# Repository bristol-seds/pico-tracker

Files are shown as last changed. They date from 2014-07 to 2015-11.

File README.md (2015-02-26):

## Bristol SEDS Pico Tracker ##

Gets its GPS position home by whatever means possible, come hell or
high water.

(Actually, come low temperatures, long paths, geopolitical
restrictions, low power etc.)

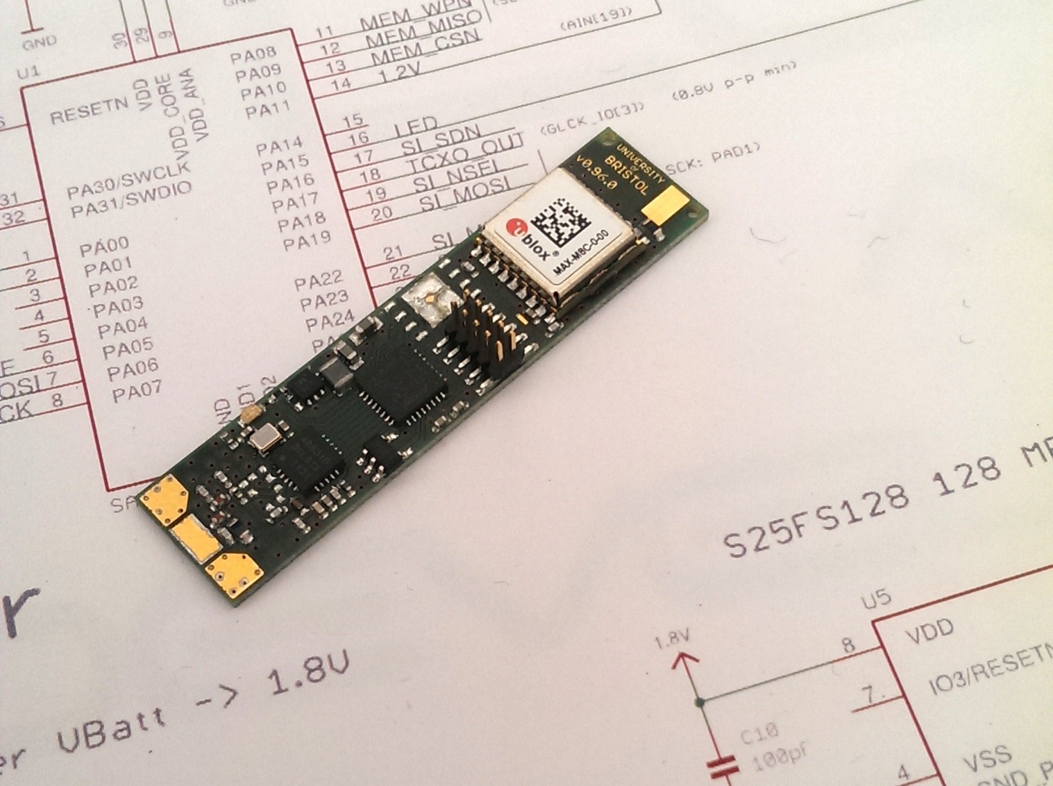
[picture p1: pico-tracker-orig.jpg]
Photo of second board revision


## Test Flight

On 31st August 2014.

## [Parts List](hardware/Parts.md)

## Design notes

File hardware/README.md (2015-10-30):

#### Hardware Revisions

Most hardware that has been built has a version number

|Version|Description|Exists/Existed|Flights used on
|----|----|----|----
|v0.96.0|Original AAA Battery. Flown with modifications to connect tcxo to mcu.|x|UBSEDS3-8?
|v0.981.0|Solar Power SPV1040. Flown with modifications simplify power circuit.|x|UBSEDS9
|v0.981.1|Minor fixes|
|v0.982.0|AAA Battery. Never fully populated, used for lab testing.|x|
|v0.982.1|Minor fixes|
|v0.984.0|First attempt at internal balloon board|
|v0.985.0|Solar Power/Primary AAA Lithium|x|UBSEDS10-11
|v0.985.1|Added DNP/0Ω between solar and MPPT set for use when only a battery is connected|
|v0.985.2|BMP180 -> MS5607 Pressure / Temperature Sensor|
|v0.985.3|Smaller holes for external thermistor|
|v0.986.0|Low Power with side mounting GPS chip antenna|
|v0.986.9|Low Power. 80x80mm Breakout|

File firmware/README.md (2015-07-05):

## Bristol Pico Tracker ##

Firmware for the Bristol Pico Tracker. Gets its GPS position home
by whatever means possible, come hell or high water.

(Actually, come low temperatures, long paths, geopolitical
restrictions, low power etc.)

## Technical Description ##

The firmware is written in C and targeted at the highly configurable
Atmel SAMD20 series of ARM Cortex M0+ micromontrollers. The code can
be built using
[GNU Tools for ARM Embedded Processors](https://launchpad.net/gcc-arm-embedded/).
See [README-samd20-gcc-blackmagic.md](README-samd20-gcc-blackmagic.md)
for more details.

## Test Suite ##

The test suite is used to run test cases on real hardware. Test cases
are written mostly in python and run using a gdb that has been built
`--with-python`. It is still a work in progress but is quite handy
when debugging.

See [test/README.md](test/README.md) for more details.

## Sources & Licensing ##

See [LICENSE.md](LICENSE.md)

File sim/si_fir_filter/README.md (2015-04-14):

## Design of the Si TX Spectral Shaping Filter

The SI contains a 17-tap digital FIR filter for use in GFSK modes.

We use this in aprs mode to filter the gpio squarewave into a sensible
afsk signal.

There's some notes in a ipython notebook `si_fir_filter.ipynp` on
this. This notebook is also used to calculate the deviation values.

## Prerequisites

```
sudo apt-get install ipython libblas-dev liblapack-dev gfortran
pip install scipy matplotlib
```

Yes you need a fortran compiler!!!

## Python Usage

`ipython notebook`

## Calcuating new coefficients

There's an awesome calculator here
[here](http://t-filter.appspot.com/fir/index.html)

## So

The python script is from
[here](http://nbviewer.ipython.org/github/unpingco/Python-for-Signal-Processing/blob/master/Filtering.ipynb)

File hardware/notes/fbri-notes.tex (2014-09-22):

\documentclass[12pt]{article}
\usepackage{graphicx}
\usepackage{color}
\usepackage{fixltx2e}
\usepackage{datatool}
\usepackage{float}
%\usepackage[showframe=true]{geometry}
\addtolength{\textwidth}{1in}
\addtolength{\textheight}{1in}
\addtolength{\evensidemargin}{0.5in}
\addtolength{\oddsidemargin}{-0.5in}
\addtolength{\topmargin}{-0.5in}
\setlength{\parindent}{0cm}

\begin{document}

\section{Hardware}

The hardware exists in two versions: a minaturised version intended
for flight and a development version intended for firmware
developement and debugging etc. The two verisons share the same
circuit diagram, and hence firmware should be generally interoperable
between the two.

However to allow detection of the hardware version PA02 is shorted to
ground on the development version while is will be pulled high
internally on the flight version.

\subsection{Dimensions}

The flight hardware has a total size of 50 x 12 mm.

Components are positioned on a 1/16 (0.0625) mm grid, with major
components on a 1/4 mm grid.

\subsection{Routing}

The board is routed with 6 mil traces for data and 6 / 16 mil traces
for power. Where nessesary the traces  All via are 0.3mm (12mil) drill.

\section{Components}

\subsection{Development}

\section{Design}

\subsection{GPS}

\subsection{ESD Proctection}

The GPS Antenna input is particularly sensitive to ESD damage. Options
for protecting against this are outlines in the uBlox hardware
intergration manual \bibitem{ublox8hw}

 One
option to protect against this is to use an LNA with integrated ESD
protection, such as.

\subsection{TCXO}

Flight UBSEDS2 clocked the Si4060 directly from a 16 MHz crystal
osciallator. This was with about 6.5pF of internal capactance from the
Si4060.

\subsection{HF Clock}

This is synthesised in the SAM D20E and used to drive the XIN input of
the SI4060. The design frequency for the XIN input is 25 - 32MHz
(30MHz by default) but UPU reports success with 16.369MHz. The maximum
output clock frequency from the SAM D20E is 48MHz so this would be a
useful design limit.

No input capacitance value is given for the XIN pin but 2pF typical is
given for out pins and this is probably about the same.

The maximum rise/fall time for 48MHz is 10ns, around 5ns would be
good, giving a knee = 100MHz.

Path inductance is maybe 10nH total (1+1+1 x 2 for pad/gnd-pad/via, 4
for trace)

Maximum output current from the SAM D20E is 1mA (with DRVSTR=0, 1.8V),
so output impedance = 1800Ω

Worst case Q
\begin{equation}
  Q = {\sqrt{10nH/2pF} \over 100} = 0.22 (good)
\end{equation}

Time constant
\begin{equation}
  tc = RC = 1800*2pF = 3.6ns (good)
\end{equation}

In any case the SI4060 tune API allows ramping up the internal
capacitance to 11pF, which will drop Q at the expense of the time
constant.

\subsection {Firmware}

Check flight WG2 on habhub for gps string formatting gone wrong

Get so much test data.

\begin{thebibliography}{9}

\bibitem{ublox8hw}
  uBlox 8 Hardware integration manual,
  http://www.u-blox.com/images/downloads/Product_Docs/MAX-M8_HardwareIntegrationManual_(UBX-13004876).pdf

\end{thebibliography}

\end{document}

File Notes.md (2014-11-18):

## PCB Weight ##

The density of FR4 is 1,850 kg/m^3. If we assume a PCB area of 12*50 =
600 mm^2...

For a 1.0mm PCB: 600 * 1.0 * 1.85 = 1.110g
For a 1.6mm PCB: 600 * 1.6 * 1.85 = 1.728g

## Contestia ##

There doesn't appear to be much documentation for contestia...

[Oh here's some](http://f1ult.free.fr/DIGIMODES/MULTIPSK/contestia_rttym_en.htm)

Really we're looking at Olivia MFSK - contestia is just a variant.

[Wikipedia](http://en.wikipedia.org/wiki/Olivia_MFSK)
[ARRL](http://www.arrl.org/olivia)

It's already implemented in dl-fldigi [here](https://github.com/jamescoxon/dl-fldigi/blob/master/src/include/jalocha/pj_mfsk.h)

(Inverse) Fast Hadamard Transform needed

## APRS ##

[some description..](http://dooce.de/dokuwiki/doku.php?id=projekte:utrak:aprs)

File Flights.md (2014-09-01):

## UBSEDS2

Launched from EMF 31/08/2014. Joint flight with CUSF (JOEY rtty/turbo)
and SUSF (UKHAS repeater).

AAA battery and surgically attached 16MHz crystal. Measured 80mA
current draw, no power saving for the ublox 6.

Revision C Atmel SAM D20 microcontrollor (bit-banged SPI)

140g free lift on a 100g Hwoyee.

4 hours battery life, much less than expected. Low temperatures?

Watchdog enabled, 64 seconds timeout (based on ULP32k oscillator, so
+-50%)

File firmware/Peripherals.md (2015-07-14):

## SAM D20 Peripherals usage

| Type | Peripheral | Function | Notes
| --- | --- | --- | ---
|*GLCK*|
||gclk0|main clock, internal osc8m|4 MHz
||gclk1|tcxo clock, fed from xosc OR osc8m
||gclk7|aprs clock, fed from gclk1, div 6 / 11
|
|*TC*||
||tc0|telemetry tick timer. 32-bit. glck1
||tc1|^^^^^
||tc2|counts cycles of tcxo. 32-bit. gclk1
||tc3|^^^^^
||tc4|unused (osc8m event source)
||tc5|telemetry pwm 16-bit glck0, ALSO aprs carrier 16-bit gclk7
|
|*EXTINT*|
||extint[5]|gps timepulse
|
|*event channels*|
||0|event source for timer 2 xosc measurement
||1|tc4 retrigger
|
|*SERCOM*||
||sercom0|spi flash
||sercom1|ublox gps
||sercom2|
||sercom3|radio|currently bitbanged as required pin layout broken in sercom

## SAM D20 Interrupts usage

| Name | Function | Priority H(0-3)L | Notes
| --- | --- | --- | ---
|TC0_IRQn|telemetry tick timer|1|latency critical for symbol timing. rate <= 1200Hz
|[GPS_SERCOM]_IRQn|gps usart rx|2|latency not so critical. rate <= 960Hz
|EIC_IRQn|timepulse|3|latency not so critical. rate = 1
|TC2_IRQn|xosc measurement done|3|latency not critical
|ADC_IRQn|adc measurement done|3|latency not critical

## Clock Layout

```
[osc8m] --> [glck0] +
                    |--> [tc5]
                    |--> [adc]
                    |--> [extint]
                    |--> [cm0+, apbs etc.]

                     |\
         [osc8m]--> 0| |
                     | | --> [glck1] +--> [tc0, telemetry tick]
tcxo --> [xosc] --> 1| |             |--> [tc2, count tcxo] <-- gps timepulse
                     |/              |--> [glck7] --> [tc5] --> si_gpio1
                      |              |--> [gps usart]
                 *USE_XOSC*

[osculp32k] --> [gclk4] --> [wdt]
```

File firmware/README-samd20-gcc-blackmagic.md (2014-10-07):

## samd20-gcc-blackmagic ##

A simple GCC setup for Atmel SAM D20 development, intended for use with the
[blackmagic debug probe](https://github.com/gsmcmullin/blackmagic).

## Prerequisites ##

[GNU Make](http://www.gnu.org/software/make/) and the following
standard utilities are required: `cat`, `echo`, `find`, `grep`,
`mkdir`, `rm`, `sed` and `tr`. If you're running any sensible desktop
linux then these will already be installed.

You will also need to aquire
[GNU Tools for ARM Embedded Processors](https://launchpad.net/gcc-arm-embedded/).

##### On Ubuntu

```
sudo add-apt-repository ppa:terry.guo/gcc-arm-embedded
sudo apt-get update && sudo apt-get install gcc-arm-none-eabi
```

###### Note about gcc-arm-embedded on Ubuntu 14.04 and later

If you are using Ubuntu 14.04 and later, please be careful because
there are packages with same name but produced by Debian and inherited
by Ubuntu. Simply follow the above 3 steps, you may end up with
gcc-arm-none-eabi from Ubuntu. So to install gcc-arm-none-eabi from
ARM, steps are:

```
1). sudo apt-get remove binutils-arm-none-eabi gcc-arm-none-eabi
2). sudo add-apt-repository ppa:terry.guo/gcc-arm-embedded
3). sudo apt-get update
4). sudo apt-get install gcc-arm-none-eabi=4-8-2014q2-0trusty10
```
Meanwhile we are working with Debian to consolidate and unify this toolchain.

## Usage ##

### Project Options ###

[`config.mk`](config.mk) allows configuation for individual
projects. In particular the `PROJECT_NAME` and `TARGET_CHIP` variables
needs to be set.

### Compiling ###

`make`

## Backmagic ##

### Download ###

Run `arm-none-eabi-gdb`. If you have set `BLACKMAGIC_PATH` in
[`config.mk`](config.mk) then gdb will attempt to connect to the
blackmagic debugger. Otherwise you can use the `blackmagic` command to
connect a `/dev/ttyACM<n>` device. For example `blackmagic 0` will
connect to a blackmagic at `/dev/ttyACM0`.

To attach to the SAM D20 chip itself you will need to run something like

```
monitor swdp_scan
attach 1
```

You can place these commands in a `gdbscript-custom` file so that in
future they will be run automatically. If `monitor swdp_scan` fails to
detect an attached SAM D20 device then you may need to upgrade the
firmware on your blackmagic to the latest version.

To download code run

```
monitor erase_mass
load
```

### Debugging ###

You can start with the gdb command

```
run
```

You might want to use the command `set confirm off` so that you're not
prompted each time. You might also want to `set mem
inaccessible-by-default off` so that you can look at memory locations
outside of RAM and ROM.

These commands can be automated by placing them in a `gdbscript-custom` file.

### Semihosting ###

You can build for semihosting by defining the `SEMIHOSTING` variable
in make. Like this:

```
make -kB SEMIHOSTING=1
```

This build will be significantly larger (in terms of RAM and ROM).

For this build, when a debugger is present at startup the
`semihost_printf`, `semihost_puts` and `semihost_putchar` functions
will print to stdio on the host. The Blackmagic Debug Probe supports
this.

## Emacs ##

The command `make emacs` can be used to quickly launch an instance of
emacs with all the relavent source code loaded.

A `TAGS` file can be generated with `make all` or `make tags`, and
this can be used to automat navigate the source code. See the
[emacs manual](https://www.gnu.org/software/emacs/manual/html_node/emacs/Tags.html)
for more details.

A Directory Local Variables File [`.dir-locals.el`](.dir-locals.el)
exists in the root of the project. This has the following effects
on emacs:

### Fixed default-directory ###

The default directory is fixed as the root of the project wherever you
are within the project. As the makefile needs to be run from the root
of the project, this means that `M+x compile` will always run the
top-level makefile no matter which file you are editing.

### Custom GDB ###

`M+x gdb` is set to use `arm-none-eabi-gdb` rather than the default GDB for your
machine.

## Other notes ##

Wherever possible use
[Function Attributes](http://gcc.gnu.org/onlinedocs/gcc/Function-Attributes.html)
and
[Variable Attrubutes](http://gcc.gnu.org/onlinedocs/gcc/Variable-Attributes.html)
rather than editing the project's linker files.

## Sources & Licensing ##

See [LICENSE.md](LICENSE-samd20-gcc-blackmagic.md)

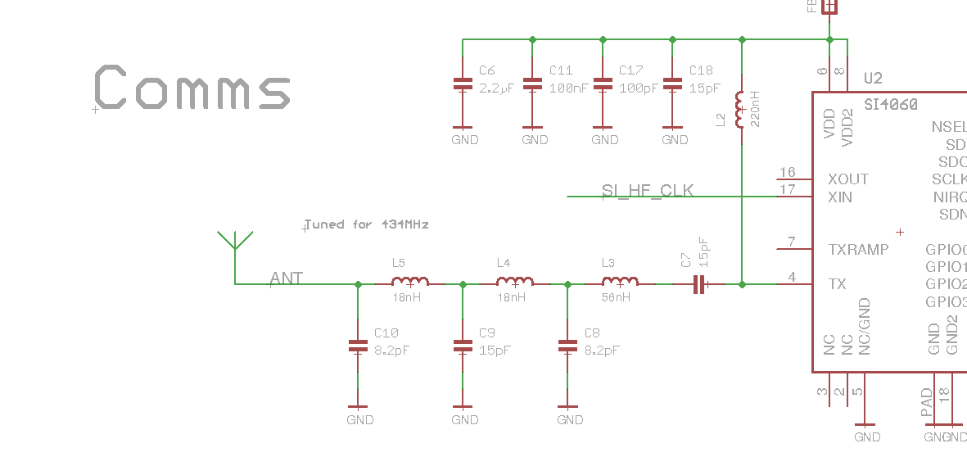
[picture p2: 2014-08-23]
hardware/pa_match.png

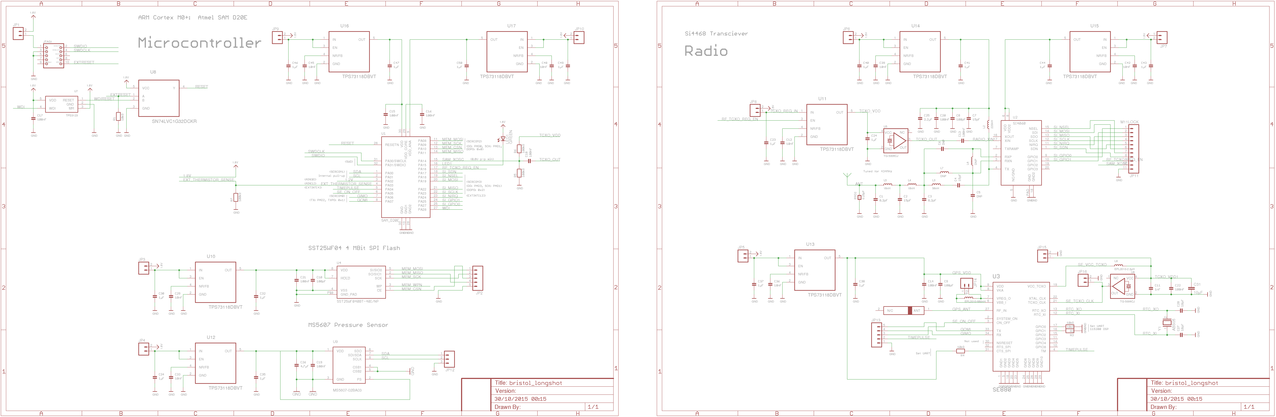
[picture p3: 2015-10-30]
hardware/low-power-breakout/bristol_longshot.sch.png

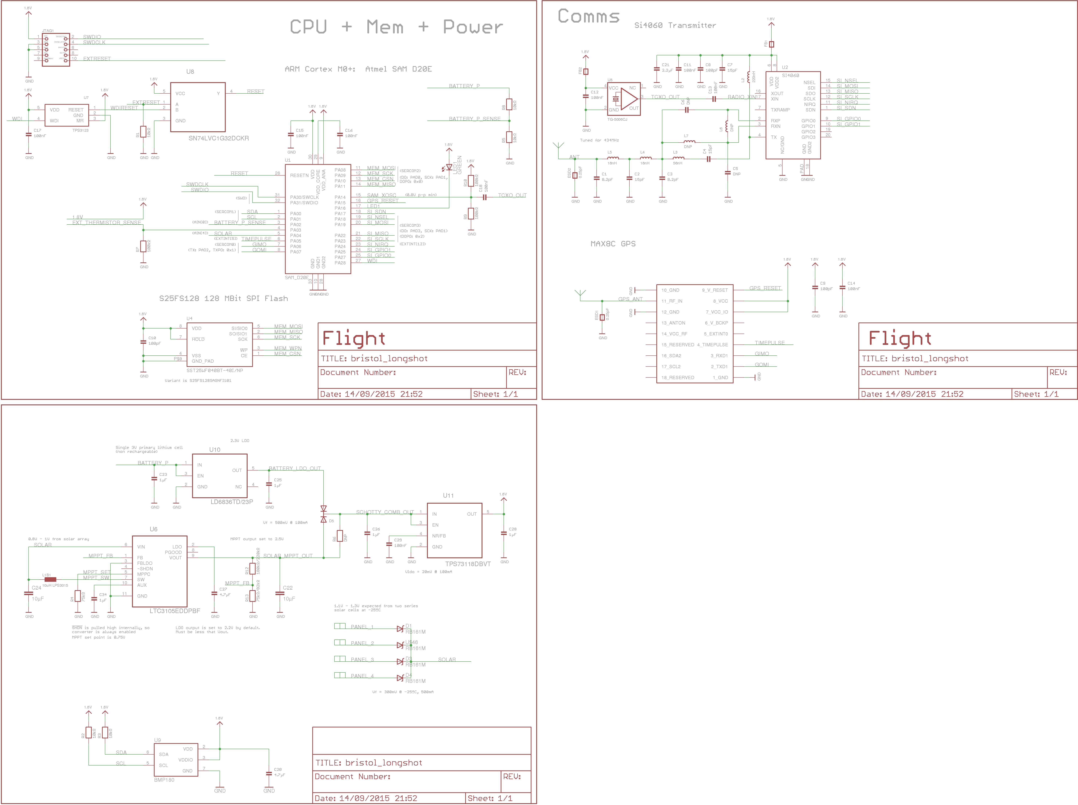
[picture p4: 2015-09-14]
hardware/main-solar/bristol_longshot.sch.png

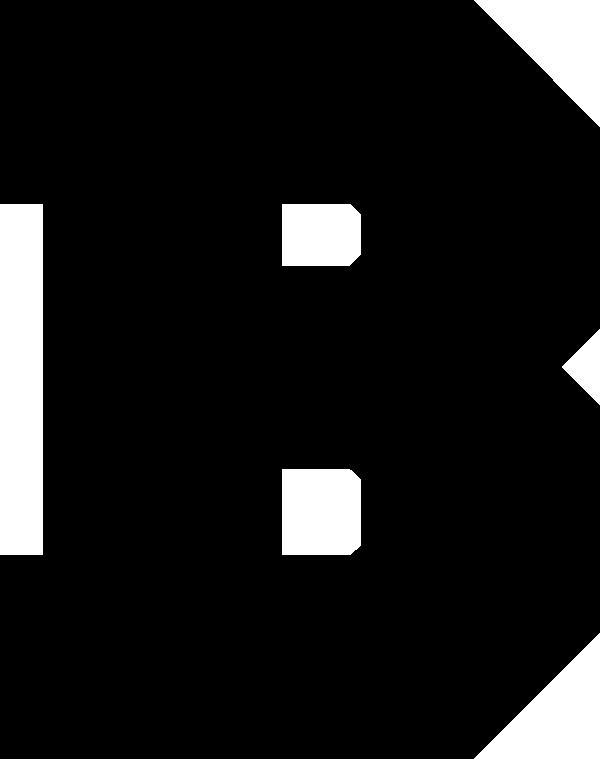
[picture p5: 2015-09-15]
hardware/graphics/b4.bmp

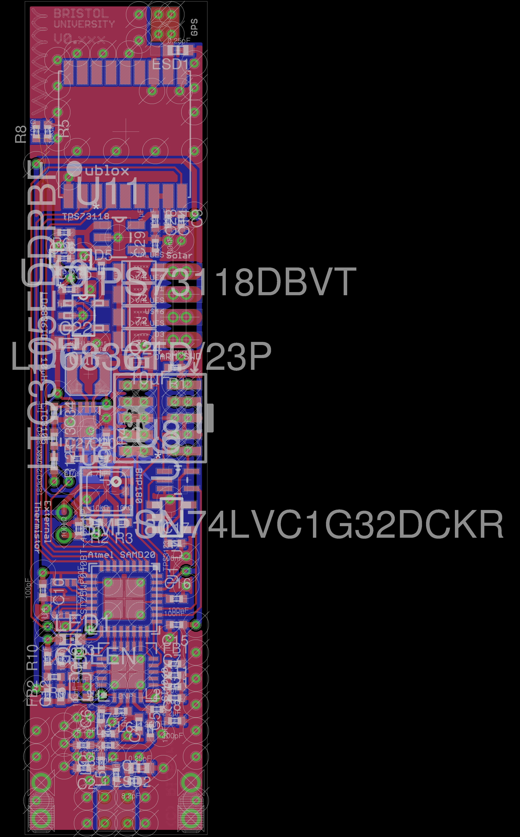
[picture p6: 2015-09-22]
hardware/main-solar/bristol_longshot.brd.png

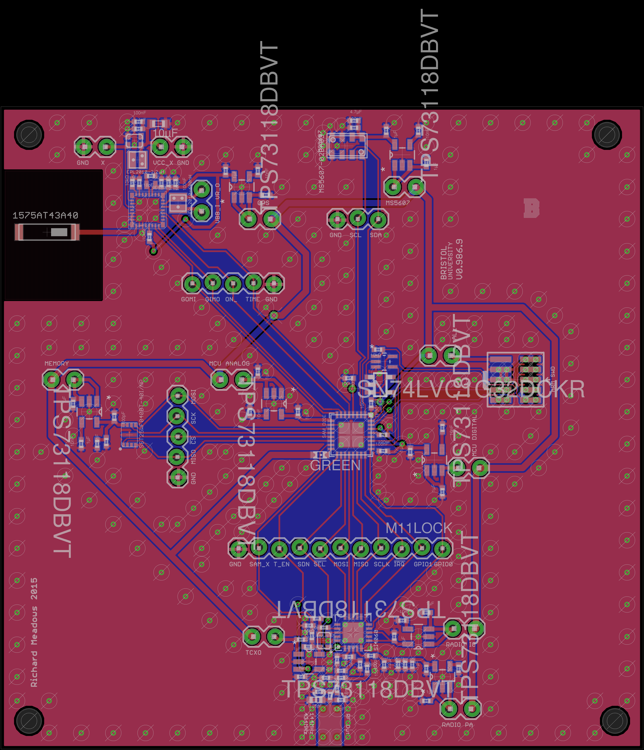
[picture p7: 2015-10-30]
hardware/low-power-breakout/bristol_longshot.brd.png

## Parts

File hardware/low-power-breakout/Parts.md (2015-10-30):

# Parts List

----
### Active

| Part | Description | Supplier | Quantity Required | Notes
| ---  | --- | --- | --- | ---
|ATSAMD20E17A-MU|ATMEL - MCU, 32BIT, CORTEX-M0+, 48MHZ, QFN-32|[2361006](http://uk.farnell.com/webapp/wcs/stores/servlet/Search?st=2361006) [556-ATSAMD20E17A-MU](http://uk.mouser.com/Search/Refine.aspx?N=1323043&Keyword=556-ATSAMD20E17A-MU)|1|U1
|SI4468-A2A-IM|SILICON LABS - RF TRANSCEIVER, 0.142-1.05GHZ, HQFN-20|[2462639](http://uk.farnell.com/webapp/wcs/stores/servlet/Search?st=2462639) [634-SI4468-A2A-IM](http://uk.mouser.com/Search/Refine.aspx?N=1323043&Keyword=634-SI4468-A2A-IM)|1|U2
| Telit SE880 | GPS | [Sequoia](http://www.sequoia.co.uk/product.php?id=1761) [Digikey](http://www.digikey.co.uk/product-detail/en/SE880GPSR22R003/943-1028-1-ND/5050348) | 1 | U3
|SST25WF040BT-40I/NP|MICROCHIP - FLASH, 4MBIT, 40MHZ, USON-8|[2414758](http://uk.farnell.com/webapp/wcs/stores/servlet/Search?st=2414758) [579-25WF040BT-40I/NP](http://uk.mouser.com/Search/Refine.aspx?N=1323043&Keyword=579-25WF040BT-40I/NP)|1|U4 memory 4Mbit
|X1G0041310008 TG-5006CJ-17H 16.369MHZ|EPSON - CRYSTAL, TCXO, TG-5006CJ-17H, 16.369 MHZ|[2405790](http://uk.farnell.com/webapp/wcs/stores/servlet/Search?st=2405790)|2|U5, U6 TCXO Si4xxx, SE880
|TPS3123J18DBVT|TEXAS INSTRUMENTS - IC, 1.62V SUPPLY MONITOR SOT-23-5|[1755607](http://uk.farnell.com/webapp/wcs/stores/servlet/Search?st=1755607) [595-TPS3123J18DBVT](http://uk.mouser.com/Search/Refine.aspx?N=1323043&Keyword=595-TPS3123J18DBVT)|1|U7 watchdog
|SN74LVC1G32DCKR|TEXAS INSTRUMENTS - IC, SINGLE 2 INPUT OR GATE, SMD|[1470880](http://uk.farnell.com/webapp/wcs/stores/servlet/Search?st=1470880) [595-SN74LVC1G32DCKR](http://uk.mouser.com/Search/Refine.aspx?N=1323043&Keyword=595-SN74LVC1G32DCKR)|1|U8 or-gate, watchdog subsystem
|MS560702BA03-50|MEASUREMENT SPECIALTIES - Pressure Sensor, Barometric, 10 mbar, 1200 mbar, QFN, 8, -40 Â°C|[2362660](http://uk.farnell.com/webapp/wcs/stores/servlet/Search?st=2362660)|1|U9 MS5607 Pressure / Temperature sensor
|ADP1607ACPZN-R7|ANALOG DEVICES - BOOST, 0.8-3.3V, 2MHZ, 1.8-3.3V, 6LFCSP|[2254940](http://uk.farnell.com/webapp/wcs/stores/servlet/Search?st=2254940)|1|U10 Boost Reg ADP1607
|TPS73118DBVT|TEXAS INSTRUMENTS - Fixed LDO Voltage Regulator, 1.7V to 5.5V, 30mV Dropout, 1.8Vout, 150mAout, SOT-23-5|[1135388](http://uk.farnell.com/webapp/wcs/stores/servlet/Search?st=1135388)|8|U11 [7xbreak] LDO for TXCO, TPS73118
|ABS05-32.768KHZ-T|ABRACON - CRYSTAL, 32.768KHZ, 12.5PF, 1.6 X 1MM|[2467859](http://uk.farnell.com/webapp/wcs/stores/servlet/Search?st=2467859)|1|Y1 32.786kHz XTAL SE880 ABS05
----

### Passives

| Part | Description | Supplier | Quantity Required | Notes
| ---  | --- | --- | --- | ---
|XFL4020-222MEC|COILCRAFT - Surface Mount Power Inductor, AEC-Q200 XFL4020 Series, 2.2 ÂµH, Â± 20%, Shielded, 0.0235 ohm, 8 A|[2289216](http://uk.farnell.com/webapp/wcs/stores/servlet/Search?st=2289216)|1|L1 2.2µH Boost Converter XFL4020-222
|0402AF-221XJLU|COILCRAFT - Surface Mount High Frequency Inductor, 0402AF Series, 220 nH, Â± 5%, 0402 [1005 Metric], 1.15 GHz|[2285640](http://uk.farnell.com/webapp/wcs/stores/servlet/Search?st=2285640)|1|L2 220nH radio
|LQG15HN56NJ02D|MURATA - INDUCTOR, 0402 CASE, 56NHÂ±5%|[1343091](http://uk.farnell.com/webapp/wcs/stores/servlet/Search?st=1343091)|1|L3 56nH rf filter
|L-07C18NJV6T|JOHANSON TECHNOLOGY - Surface Mount High Frequency Inductor, L-07C Series, 18 nH, Â± 5%, 0402 [1005 Metric], 0.65 ohm|[1865775](http://uk.farnell.com/webapp/wcs/stores/servlet/Search?st=1865775)|1|L4, L5 18nH rf filter
| L6, L7 | DNP ||| si4xxx rx
|EPL2010-681MLB|COILCRAFT - Surface Mount Power Inductor, EPL2010 Series, 680 nH, Â± 20%, Shielded, 0.07 ohm, 1.94 A|[2287364](http://uk.farnell.com/webapp/wcs/stores/servlet/Search?st=2287364)|1|L8 SE880 EPL2010-681
|EPL2010-222MLB|COILCRAFT - Surface Mount Power Inductor, EPL2010 Series, 2.2 ÂµH, Â± 20%, Shielded, 0.222 ohm, 978 mA|[2287369](http://uk.farnell.com/webapp/wcs/stores/servlet/Search?st=2287369)|1|L9 SE880 EPL2010-22222
|MC00625W0402110K|MULTICOMP - Surface Mount Chip Resistor, Thick Film, MC Series, 10 kohm, 62.5 mW, Â± 1%, 50 V|[1358069](http://uk.farnell.com/webapp/wcs/stores/servlet/Search?st=1358069)|4|R1, R2, R3, R4 10k
|CRG0402F100K|TE CONNECTIVITY - Surface Mount Chip Resistor, Thick Film, CRG Series, 100 kohm, 63 mW, Â± 1%, 50 V|[2331442](http://uk.farnell.com/webapp/wcs/stores/servlet/Search?st=2331442)|2|R5, R6 100k
|CPF-A-0402B100KE1|TE CONNECTIVITY - Surface Mount Chip Resistor, Thin Film, AEC-Q200 CPF-A Series, 100 kohm, 62.5 mW, Â± 0.1%, 25 V|[2483832](http://uk.farnell.com/webapp/wcs/stores/servlet/Search?st=2483832)|2|R7, R9 100k 0.1%
|ERA2AEB433X|PANASONIC ELECTRONIC COMPONENTS - Surface Mount Chip Resistor, Metal Film, AEC-Q200 ERA Series, 43 kohm, 63 mW, Â± 0.1%, 25 V|[2324785](http://uk.farnell.com/webapp/wcs/stores/servlet/Search?st=2324785)|1|R8 43k 0.1%
|GRM1555C1H8R2CA01D|MURATA - SMD Multilayer Ceramic Capacitor, GRM Series, 8.2 pF, Â± 0.25pF, C0G / NP0, 50 V, 0402 [1005 Metric]|[1828874](http://uk.farnell.com/webapp/wcs/stores/servlet/Search?st=1828874)|2|C1, C3 8.2pF
|MC0402N150J500CT|MULTICOMP - SMD Multilayer Ceramic Capacitor, MC Series, 15 pF, Â± 5%, C0G / NP0, 50 V, 0402 [1005 Metric]|[1758945](http://uk.farnell.com/webapp/wcs/stores/servlet/Search?st=1758945)|3|C2, C4, C7 15pF
| C5, C6 | DNP ||| si4xxx rx
|MC0402N101J500CT|MULTICOMP - SMD Multilayer Ceramic Capacitor, MC Series, 100 pF, Â± 5%, C0G / NP0, 50 V, 0402 [1005 Metric]|[1758969](http://uk.farnell.com/webapp/wcs/stores/servlet/Search?st=1758969)|3|C8, C9, C10 100pF
|MC0402B102K500CT|MULTICOMP - SMD Multilayer Ceramic Capacitor, MC Series, 1000 pF, Â± 10%, X7R, 50 V, 0402 [1005 Metric]|[1758991](http://uk.farnell.com/webapp/wcs/stores/servlet/Search?st=1758991)|1|C11 1nF
|GRM155R71E103KA01D|MURATA - SMD Multilayer Ceramic Capacitor, GRM Series, 0.01 ÂµF, Â± 10%, X7R, 25 V, 0402 [1005 Metric]|[8819734](http://uk.farnell.com/webapp/wcs/stores/servlet/Search?st=8819734)|8|C12 [7xbreak] 10nF
|MC0402X104K100CT|MULTICOMP - SMD Multilayer Ceramic Capacitor, MC Series, 0.1 ÂµF, Â± 10%, X5R, 10 V, 0402 [1005 Metric]|[1759380](http://uk.farnell.com/webapp/wcs/stores/servlet/Search?st=1759380)|10|C13, C14, C15, C16, C17, C18, C19, C20, C21, C22 100nF
|GRM155R61E105KA12D|MURATA - SMD Multilayer Ceramic Capacitor, GRM Series, 1 ÂµF, Â± 10%, X5R, 25 V, 0402 [1005 Metric]|[2218855](http://uk.farnell.com/webapp/wcs/stores/servlet/Search?st=2218855)|16|[7xbreak] C23, C24 1µF
|GRM155R60J225ME15D|MURATA - SMD Multilayer Ceramic Capacitor, GRM Series, 2.2 ÂµF, Â± 20%, X5R, 6.3 V, 0402 [1005 Metric]|[2362088](http://uk.farnell.com/webapp/wcs/stores/servlet/Search?st=2362088)|1|C25 Radio Bypass 2.2µF
|C1005X5R0J475M050BC|TDK - SMD Multilayer Ceramic Capacitor, C Series, 4.7 ÂµF, Â± 20%, X5R, 6.3 V, 0402 [1005 Metric]|[2309027](http://uk.farnell.com/webapp/wcs/stores/servlet/Search?st=2309027)|1|C26 MS5607 Bypass 4.7µF
|MC0402N180J500CT|MULTICOMP - SMD Multilayer Ceramic Capacitor, MC Series, 18 pF, Â± 5%, C0G / NP0, 50 V, 0402 [1005 Metric]|[1758947](http://uk.farnell.com/webapp/wcs/stores/servlet/Search?st=1758947)|2|C27, C28 18pF SE880 Y1 Load
|06036D106MAT2A|AVX - SMD Multilayer Ceramic Capacitor, 10 ÂµF, Â± 20%, X5R, 6.3 V, 0603 [1608 Metric]|[1833804](http://uk.farnell.com/webapp/wcs/stores/servlet/Search?st=1833804)|3|C29, C30, C31 Boost in, out 10µF 0603
|GRM31CR60J107ME39L.|MURATA - SMD Multilayer Ceramic Capacitor, GRM Series, 100 ÂµF, Â± 20%, X5R, 6.3 V, 1206 [3216 Metric]|[1735535](http://uk.farnell.com/webapp/wcs/stores/servlet/Search?st=1735535)|1|C32 100µF optional
| 1575AT43A40 | GPS Antenna | [Proto-pic](http://proto-pic.co.uk/antenna-gps-chip-scale/) | 1 | A1 1.575GHz

----

### Misc

| Part | Description | Supplier | Quantity Required | Notes
| ---  | --- | --- | --- | ---
|20021121-00010C4LF.|FCI - Board-To-Board Connector, Right Angle, Minitek127 20021121 Series, Surface Mount, Header, 10|[1865279](http://uk.farnell.com/webapp/wcs/stores/servlet/Search?st=1865279) [649-202112100010C4LF](http://uk.mouser.com/Search/Refine.aspx?N=1323043&Keyword=649-202112100010C4LF)|1|JTAG1
|742792731|WURTH ELEKTRONIK - FERRITE BEAD, 0.09OHM, 1.2A, 0402|[1961698](http://uk.farnell.com/webapp/wcs/stores/servlet/Search?st=1961698)|3|FB1, FB2, FB3
|CG0603MLC-05LE|BOURNS - ESD Protection Device, 25 V, 5 V, 0603, 2|[1828732](http://uk.farnell.com/webapp/wcs/stores/servlet/Search?st=1828732)|0|ESD1, ESD2
|B57861S0103F040|EPCOS - THERMISTOR, 10K, 1%, NTC, RAD|[679446](http://uk.farnell.com/webapp/wcs/stores/servlet/Search?st=679446)|1|External Thermistor
| | Antenna Wire | [ebay](http://www.ebay.co.uk/itm/Ernie-Ball-Custom-Gauge-Guitar-Single-Strings-Electric-or-Acoustic-Pack-6-13-/360959212478 ) | 1 | Ernie Ball .013
| | Energizer Ultimate Lithium AAA | [datasheet](http://data.energizer.com/PDFs/l92.pdf) | 1 | ~1200mAh
| | Energizer Ultimate Lithium AA | [datasheet](http://data.energizer.com/PDFs/l91.pdf) | 0 | ~3000mAh
|FFSD-05-D-06.00-01-N|SAMTEC - RIBBON CABLE, IDC, 152.4MM, GREY, 10WAY|[1667659](http://uk.farnell.com/webapp/wcs/stores/servlet/Search?st=1667659)|0|10way 1.27mm

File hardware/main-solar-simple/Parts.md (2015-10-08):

# Parts List

** Parts for HF Section not yet included **

----
### Active

| Part | Description | Supplier | Quantity Required | Notes
| ---  | --- | --- | --- | ---
|ATSAMD20E17A-MU|ATMEL - MCU, 32BIT, CORTEX-M0+, 48MHZ, QFN-32|[2361006](http://uk.farnell.com/webapp/wcs/stores/servlet/Search?st=2361006) [556-ATSAMD20E17A-MU](http://uk.mouser.com/Search/Refine.aspx?N=1323043&Keyword=556-ATSAMD20E17A-MU)|1|U1
|SI4468-A2A-IM|SILICON LABS - RF TRANSCEIVER, 0.142-1.05GHZ, HQFN-20|[2462639](http://uk.farnell.com/webapp/wcs/stores/servlet/Search?st=2462639) [634-SI4468-A2A-IM](http://uk.mouser.com/Search/Refine.aspx?N=1323043&Keyword=634-SI4468-A2A-IM)|1|U2
| UBLOX MAX-8C | GPS | [HAB Supplies](http://ava.upuaut.net/store/index.php?route=product/product&path=59_64&product_id=108) | 1 | U3
|SST25WF040BT-40I/NP|MICROCHIP - FLASH, 4MBIT, 40MHZ, USON-8|[2414758](http://uk.farnell.com/webapp/wcs/stores/servlet/Search?st=2414758) [579-25WF040BT-40I/NP](http://uk.mouser.com/Search/Refine.aspx?N=1323043&Keyword=579-25WF040BT-40I/NP)|1|U4 memory 4Mbit
|X1G0041310008 TG-5006CJ-17H 16.369MHZ|EPSON - CRYSTAL, TCXO, TG-5006CJ-17H, 16.369 MHZ|[2405790](http://uk.farnell.com/webapp/wcs/stores/servlet/Search?st=2405790)|1|U5 TCXO Si4xxx
|LTC3105EDD#PBF|LINEAR TECHNOLOGY - BOOST, 400MA, MPPC, 10DFN|[1898600](http://uk.farnell.com/webapp/wcs/stores/servlet/Search?st=1898600)|1|U6 Solar Energy Boost Converter
|TPS3123J18DBVT|TEXAS INSTRUMENTS - IC, 1.62V SUPPLY MONITOR SOT-23-5|[1755607](http://uk.farnell.com/webapp/wcs/stores/servlet/Search?st=1755607) [595-TPS3123J18DBVT](http://uk.mouser.com/Search/Refine.aspx?N=1323043&Keyword=595-TPS3123J18DBVT)|1|U7 watchdog
|SN74LVC1G32DCKR|TEXAS INSTRUMENTS - IC, SINGLE 2 INPUT OR GATE, SMD|[1470880](http://uk.farnell.com/webapp/wcs/stores/servlet/Search?st=1470880) [595-SN74LVC1G32DCKR](http://uk.mouser.com/Search/Refine.aspx?N=1323043&Keyword=595-SN74LVC1G32DCKR)|1|U8 or-gate, watchdog subsystem
|MS560702BA03-50|MEASUREMENT SPECIALTIES - Pressure Sensor, QFN, 8, -40 Â°C, 85 Â°C, 1.8 V, 3.6 V|[2362660](http://uk.farnell.com/webapp/wcs/stores/servlet/Search?st=2362660)|1|U9 MS5607 Pressure / Temperature sensor
|RB161M-20TR|ROHM - Small Signal Schottky Diode, Single, 25 V, 1 A, 350 mV, 30 A, 125 Â°C|[1525484](http://uk.farnell.com/webapp/wcs/stores/servlet/Search?st=1525484)|5|D1, D2, D3, D4, D5 Small signal schotty diode
----

### Passives

| Part | Description | Supplier | Quantity Required | Notes
| ---  | --- | --- | --- | ---
|LPS3015-103MRB|COILCRAFT - Surface Mount Power Inductor, AEC-Q200 LPS3015 Series, 10 ÂµH, Â± 20%, Shielded, 0.44 ohm, 550 mA|[2408024](http://uk.farnell.com/webapp/wcs/stores/servlet/Search?st=2408024)|1|L11 10µH LPS3015
|0402AF-221XJLU|COILCRAFT - Surface Mount High Frequency Inductor, 0402AF Series, 220 nH, Â± 5%, 0402 [1005 Metric], 1.15 GHz|[2285640](http://uk.farnell.com/webapp/wcs/stores/servlet/Search?st=2285640)|1|L2 220nH radio
|LQG15HN56NJ02D|MURATA - INDUCTOR, 0402 CASE, 56NHÂ±5%|[1343091](http://uk.farnell.com/webapp/wcs/stores/servlet/Search?st=1343091)|1|L3 56nH rf filter
|L-07C18NJV6T|JOHANSON TECHNOLOGY - Surface Mount High Frequency Inductor, L-07C Series, 18 nH, Â± 5%, 0402 [1005 Metric], 0.65 ohm|[1865775](http://uk.farnell.com/webapp/wcs/stores/servlet/Search?st=1865775)|1|L4, L5 18nH rf filter
| L6, L7 | DNP ||| si4xxx rx
|MC00625W0402110K|MULTICOMP - Surface Mount Chip Resistor, Thick Film, MC Series, 10 kohm, 62.5 mW, Â± 1%, 50 V|[1358069](http://uk.farnell.com/webapp/wcs/stores/servlet/Search?st=1358069)|7|R1, R2, R3 10k
|ERA2AED104X|PANASONIC ELECTRONIC COMPONENTS - Surface Mount Chip Resistor, Metal Film, AEC-Q200 ERA Series, 100 kohm, 63 mW, Â± 0.5%, 25 V|[2324718](http://uk.farnell.com/webapp/wcs/stores/servlet/Search?st=2324718)|1|R4 100k precise
|CRG0402F100K|TE CONNECTIVITY - Surface Mount Chip Resistor, Thick Film, CRG Series, 100 kohm, 63 mW, Â± 1%, 50 V|[2331442](http://uk.farnell.com/webapp/wcs/stores/servlet/Search?st=2331442)|2|R5, R6 100k
|RC0402JR-070RL|YAGEO (PHYCOMP) - Surface Mount Chip Resistor, Thick Film, RC Series, 0 ohm, 62.5 mW, Â± 5%, 50 V, 0402 [1005 Metric]|[9232516](http://uk.farnell.com/webapp/wcs/stores/servlet/Search?st=9232516)|1|R7 Bridge 0Ω
| R8 | DNP ||| connect MPPT set when battery only is used
|CRG0402F82K|TE CONNECTIVITY - Surface Mount Chip Resistor, Thick Film, CRG Series, 82 kohm, 63 mW, Â± 1%, 50 V, 0402 [1005 Metric]|[2331569](http://uk.farnell.com/webapp/wcs/stores/servlet/Search?st=2331569)|3|R10, R12, R14 LTC3105 82k
|CRG0402F68K|TE CONNECTIVITY - Surface Mount Chip Resistor, Thick Film, CRG Series, 68 kohm, 63 mW, Â± 1%, 50 V, 0402 [1005 Metric]|[2331557](http://uk.farnell.com/webapp/wcs/stores/servlet/Search?st=2331557)|1|R11 LTC3105 FB 68k
|MC00625W0402156K|MULTICOMP - Surface Mount Chip Resistor, Thick Film, MC Series, 56 kohm, 62.5 mW, Â± 1%, 50 V|[1358089](http://uk.farnell.com/webapp/wcs/stores/servlet/Search?st=1358089)|1|R13 LTC3105 LDOFB 56k
|GRM1555C1H8R2CA01D|MURATA - SMD Multilayer Ceramic Capacitor, GRM Series, 8.2 pF, Â± 0.25pF, C0G / NP0, 50 V, 0402 [1005 Metric]|[1828874](http://uk.farnell.com/webapp/wcs/stores/servlet/Search?st=1828874)|2|C1, C3 8.2pF
|MC0402N150J500CT|MULTICOMP - SMD Multilayer Ceramic Capacitor, MC Series, 15 pF, Â± 5%, C0G / NP0, 50 V, 0402 [1005 Metric]|[1758945](http://uk.farnell.com/webapp/wcs/stores/servlet/Search?st=1758945)|3|C2, C4, C7 15pF
| C5, C6 | DNP ||| si4xxx rx
|MC0402N101J500CT|MULTICOMP - SMD Multilayer Ceramic Capacitor, MC Series, 100 pF, Â± 5%, C0G / NP0, 50 V, 0402 [1005 Metric]|[1758969](http://uk.farnell.com/webapp/wcs/stores/servlet/Search?st=1758969)|3|C8, C9, C10 100pF
|MC0402X104K100CT|MULTICOMP - SMD Multilayer Ceramic Capacitor, MC Series, 0.1 ÂµF, Â± 10%, X5R, 10 V, 0402 [1005 Metric]|[1759380](http://uk.farnell.com/webapp/wcs/stores/servlet/Search?st=1759380)|9|C11, C12, C13, C14, C15, C16, C17, C18, C19 100nF
|GRM155R61E105KA12D|MURATA - SMD Multilayer Ceramic Capacitor, GRM Series, 1 ÂµF, Â± 10%, X5R, 25 V, 0402 [1005 Metric]|[2218855](http://uk.farnell.com/webapp/wcs/stores/servlet/Search?st=2218855)|1|C20 LTC3015 AUX 1µF
|GRM155R60J225ME15D|MURATA - SMD Multilayer Ceramic Capacitor, GRM Series, 2.2 ÂµF, Â± 20%, X5R, 6.3 V, 0402 [1005 Metric]|[2362088](http://uk.farnell.com/webapp/wcs/stores/servlet/Search?st=2362088)|1|C21 Radio Bypass 2.2µF
|C1005X5R0J475M050BC|TDK - SMD Multilayer Ceramic Capacitor, C Series, 4.7 ÂµF, Â± 20%, X5R, 6.3 V, 0402 [1005 Metric]|[2309027](http://uk.farnell.com/webapp/wcs/stores/servlet/Search?st=2309027)|2|C22, C23 MS5607 Bypass, LTC3105 LDO 4.7µF
|06036D106MAT2A|AVX - SMD Multilayer Ceramic Capacitor, 10 ÂµF, Â± 20%, X5R, 6.3 V, 0603 [1608 Metric]|[1833804](http://uk.farnell.com/webapp/wcs/stores/servlet/Search?st=1833804)|2|C24, C25 LTC3105 in, out 10µF 0603

----

### Misc

| Part | Description | Supplier | Quantity Required | Notes
| ---  | --- | --- | --- | ---
|20021121-00010C4LF.|FCI - Board-To-Board Connector, Minitek127 20021121 Series, Surface Mount, Header, 10, 1.27 mm|[1865279](http://uk.farnell.com/webapp/wcs/stores/servlet/Search?st=1865279) [649-202112100010C4LF](http://uk.mouser.com/Search/Refine.aspx?N=1323043&Keyword=649-202112100010C4LF)|1|JTAG1
|742792731|WURTH ELEKTRONIK - FERRITE BEAD, 0.09OHM, 1.2A, 0402|[1961698](http://uk.farnell.com/webapp/wcs/stores/servlet/Search?st=1961698)|2|FB1, FB2
|CG0603MLC-05LE|BOURNS - ESD Protection Device, 25 V, 5 V, 0603, 2|[1828732](http://uk.farnell.com/webapp/wcs/stores/servlet/Search?st=1828732)|0|ESD1, ESD2
|B57861S0103F040|EPCOS - THERMISTOR, 10K, 1%, NTC, RAD|[679446](http://uk.farnell.com/webapp/wcs/stores/servlet/Search?st=679446)|1|External Thermistor
| | Antenna Wire | [ebay](http://www.ebay.co.uk/itm/Ernie-Ball-Custom-Gauge-Guitar-Single-Strings-Electric-or-Acoustic-Pack-6-13-/360959212478 ) | 1 | Ernie Ball .013
| | Energizer Ultimate Lithium AAA | [datasheet](http://data.energizer.com/PDFs/l92.pdf) | 1 | ~1200mAh

----

## AAA Hardware

| ID | Part Number | Description | Supplier | Order Code | Quantity
| --- | --- | --- | --- | --- | ---
|FFSD-05-D-06.00-01-N|SAMTEC - RIBBON CABLE, IDC, 152.4MM, GREY, 10WAY|[1667659](http://uk.farnell.com/webapp/wcs/stores/servlet/Search?st=1667659)|0|10way 1.27mm

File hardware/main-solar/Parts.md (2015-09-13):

# Parts List

** Parts for HF Section not yet included **

----
### Active

| Part | Description | Supplier | Quantity Required | Notes
| ---  | --- | --- | --- | ---
|ATSAMD20E17A-MU|ATMEL - MCU, 32BIT, CORTEX-M0+, 48MHZ, QFN-32|[2361006](http://uk.farnell.com/webapp/wcs/stores/servlet/Search?st=2361006) [556-ATSAMD20E17A-MU](http://uk.mouser.com/Search/Refine.aspx?N=1323043&Keyword=556-ATSAMD20E17A-MU)|1|U1
|SI4468-A2A-IM|SILICON LABS - RF TRANSCEIVER, 0.142-1.05GHZ, HQFN-20|[2462639](http://uk.farnell.com/webapp/wcs/stores/servlet/Search?st=2462639) [634-SI4468-A2A-IM](http://uk.mouser.com/Search/Refine.aspx?N=1323043&Keyword=634-SI4468-A2A-IM)|1|U2
| UBLOX MAX-8C | GPS | [HAB Supplies](http://ava.upuaut.net/store/index.php?route=product/product&path=59_64&product_id=108) | 1 | U3
|SST25WF040BT-40I/NP|MICROCHIP - FLASH, 4MBIT, 40MHZ, USON-8|[2414758](http://uk.farnell.com/webapp/wcs/stores/servlet/Search?st=2414758) [579-25WF040BT-40I/NP](http://uk.mouser.com/Search/Refine.aspx?N=1323043&Keyword=579-25WF040BT-40I/NP)|1|U4 memory 4mbit
|X1G0041310008 TG-5006CJ-17H 16.369MHZ|EPSON - CRYSTAL, TCXO, TG-5006CJ-17H, 16.369 MHZ|[2405790](http://uk.farnell.com/webapp/wcs/stores/servlet/Search?st=2405790)|2|U5, U6 TCXO Si4xxx, SE880
|TPS3123J18DBVT|TEXAS INSTRUMENTS - IC, 1.62V SUPPLY MONITOR SOT-23-5|[1755607](http://uk.farnell.com/webapp/wcs/stores/servlet/Search?st=1755607) [595-TPS3123J8DBVT](http://uk.mouser.com/Search/Refine.aspx?N=1323043&Keyword=595-TPS3123J8DBVT)|1|U7 watchdog
|SN74LVC1G32DCKR|TEXAS INSTRUMENTS - IC, SINGLE 2 INPUT OR GATE, SMD|[1470880](http://uk.farnell.com/webapp/wcs/stores/servlet/Search?st=1470880) [595-SN74LVC1G32DCKR](http://uk.mouser.com/Search/Refine.aspx?N=1323043&Keyword=595-SN74LVC1G32DCKR)|1|U8 or-gate, watchdog subsystem
|LTC3105EDD#PBF|LINEAR TECHNOLOGY - BOOST, 400MA, MPPC, 10DFN|[1898600](http://uk.farnell.com/webapp/wcs/stores/servlet/Search?st=1898600)|0|Solar Energy Boost Converter
|LD6836TD/23P|NXP - LDO, 5.5V, 0.09VDO, 0.3A, 2.3V, 5SOT753|[2308325](http://uk.farnell.com/webapp/wcs/stores/servlet/Search?st=2308325)|0|2.3V LDO regulator
|TPS73118DBVT|TEXAS INSTRUMENTS - V REG LDO 0.15A +1.8V, SMD, 73118|[1135388](http://uk.farnell.com/webapp/wcs/stores/servlet/Search?st=1135388)|0|1.8V LDO regulator
|RB161M-20TR|ROHM - Small Signal Schottky Diode, Single, 25 V, 1 A, 350 mV, 30 A, 125 Â°C|[1525484](http://uk.farnell.com/webapp/wcs/stores/servlet/Search?st=1525484)|0|D2, D3, D4 Small signal schotty diode
|BAT54CLT1G|ON SEMICONDUCTOR - Small Signal Schottky Diode, Dual Common Cathode, 30 V, 200 mA, 800 mV, 600 mA, 125 Â°C|[1431112](http://uk.farnell.com/webapp/wcs/stores/servlet/Search?st=1431112)|0|Dual common-cathode schotty diode
----

### Passives

| Part | Description | Supplier | Quantity Required | Notes
| ---  | --- | --- | --- | ---
|LPS3015-103MRB|COILCRAFT - Surface Mount Power Inductor, AEC-Q200 LPS3015 Series, 10 ÂµH, Â± 20%, Shielded, 0.44 ohm|[2408024](http://uk.farnell.com/webapp/wcs/stores/servlet/Search?st=2408024)|1|L11 10µH LPS3015
|0402AF-221XJLU|COILCRAFT - Surface Mount High Frequency Inductor, 0402AF Series, 220 nH, Â± 5%, 0402 [1005 Metric]|[2285640](http://uk.farnell.com/webapp/wcs/stores/servlet/Search?st=2285640)|1|L2 220nH radio
|LQG15HN56NJ02D|MURATA - INDUCTOR, 0402 CASE, 56NHÂ±5%|[1343091](http://uk.farnell.com/webapp/wcs/stores/servlet/Search?st=1343091)|1|L3 56nH rf filter
|L-07C18NJV6T|JOHANSON TECHNOLOGY - Surface Mount High Frequency Inductor, L-07C Series, 18 nH, Â± 5%, 0402 [1005 Metric]|[1865775](http://uk.farnell.com/webapp/wcs/stores/servlet/Search?st=1865775)|1|L4, L5 18nH rf filter
| L6, L7 | DNP ||| si4xxx rx
|SRN2512-2R2M|BOURNS - Surface Mount Power Inductor, SRN2512 Series, 2.2 ÂµH, Â± 20%, Semishielded, 0.102 ohm, 2.3 A|[2428203](http://uk.farnell.com/webapp/wcs/stores/servlet/Search?st=2428203)|2|L8, L9 inductor for buck regulators 2.2µH
|MC00625W0402110K|MULTICOMP - Surface Mount Chip Resistor, Thick Film, MC Series, 10 kohm, 62.5 mW, Â± 1%, 50 V|[1358069](http://uk.farnell.com/webapp/wcs/stores/servlet/Search?st=1358069)|7|R1, R2, R3, R4, R5, R6, R7 10k
|CRG0402F22K|TE CONNECTIVITY - Surface Mount Chip Resistor, Thick Film, CRG Series, 22 kohm, 63 mW, Â± 1%, 50 V|[2331489](http://uk.farnell.com/webapp/wcs/stores/servlet/Search?st=2331489)|1|R8 22k
|CRG0402F100K|TE CONNECTIVITY - Surface Mount Chip Resistor, Thick Film, CRG Series, 100 kohm, 63 mW, Â± 1%, 50 V|[2331442](http://uk.farnell.com/webapp/wcs/stores/servlet/Search?st=2331442)|2|R9, R10 100k
|CRG0402F1K0|TE CONNECTIVITY - Surface Mount Chip Resistor, Thick Film, CRG Series, 1 kohm, 63 mW, Â± 1%, 50 V|[2331474](http://uk.farnell.com/webapp/wcs/stores/servlet/Search?st=2331474)|1|R11 Mpp-set 1k
|CRG0402F220K|TE CONNECTIVITY - Surface Mount Chip Resistor, Thick Film, CRG Series, 220 kohm, 63 mW, Â± 1%, 50 V|[2331487](http://uk.farnell.com/webapp/wcs/stores/servlet/Search?st=2331487)|1|R12A Vctrl-up 4.6V 220k
|CRG0402F180K|TE CONNECTIVITY - Surface Mount Chip Resistor, Thick Film, CRG Series, 180 kohm, 63 mW, Â± 1%, 50 V|[2331468](http://uk.farnell.com/webapp/wcs/stores/servlet/Search?st=2331468)|1|R12B Vctrl-up 4.25V 180k
|CRG0402F82K|TE CONNECTIVITY - Surface Mount Chip Resistor, Thick Film, CRG Series, 82 kohm, 63 mW, Â± 1%, 50 V|[2331569](http://uk.farnell.com/webapp/wcs/stores/servlet/Search?st=2331569)|1|R13A Vctrl-down 4.6V 82k
|MCWR04X7502FTL|MULTICOMP - Surface Mount Chip Resistor, Thick Film, MCWR Series, 75 kohm, 62.5 mW, Â± 1%, 50 V|[2447215](http://uk.farnell.com/webapp/wcs/stores/servlet/Search?st=2447215)|1|R13B Vctrl-down 4.25V 75k
|CRG0402F2K2|TE CONNECTIVITY - Surface Mount Chip Resistor, Thick Film, CRG Series, 2.2 kohm, 63 mW, Â± 1%, 50 V|[2331502](http://uk.farnell.com/webapp/wcs/stores/servlet/Search?st=2331502)|1|R14 Rprog 2.2k
|RC0402JR-070RL|YAGEO (PHYCOMP) - Surface Mount Chip Resistor, Thick Film, RC Series, 0 ohm, 62.5 mW, Â± 5%, 50 V|[9232516](http://uk.farnell.com/webapp/wcs/stores/servlet/Search?st=9232516)|1|R15 Bridge 0Ω
|GRM1555C1H8R2CA01D|MURATA - SMD Multilayer Ceramic Capacitor, GRM Series, 8.2 pF, Â± 0.25pF, C0G / NP0, 50 V|[1828874](http://uk.farnell.com/webapp/wcs/stores/servlet/Search?st=1828874)|2|C1, C3 8.2pF
|MC0402N150J500CT|MULTICOMP - SMD Multilayer Ceramic Capacitor, MC Series, 15 pF, Â± 5%, C0G / NP0, 50 V, 0402 [1005 Metric]|[1758945](http://uk.farnell.com/webapp/wcs/stores/servlet/Search?st=1758945)|3|C2, C4, C7 15pF
| C5, C6 | DNP ||| si4xxx rx
|MC0402N101J500CT|MULTICOMP - SMD Multilayer Ceramic Capacitor, MC Series, 100 pF, Â± 5%, C0G / NP0, 50 V, 0402 [1005 Metric]|[1758969](http://uk.farnell.com/webapp/wcs/stores/servlet/Search?st=1758969)|3|C8, C9, C10 100pF
|MC0402X104K100CT|MULTICOMP - SMD Multilayer Ceramic Capacitor, MC Series, 0.1 ÂµF, Â± 10%, X5R, 10 V, 0402 [1005 Metric]|[1759380](http://uk.farnell.com/webapp/wcs/stores/servlet/Search?st=1759380)|10|C11, C12, C13, C14, C15, C16, C17, C18, C19, C20 100nF
|GRM155R60J225ME15D|MURATA - SMD Multilayer Ceramic Capacitor, GRM Series, 2.2 ÂµF, Â± 20%, X5R, 6.3 V, 0402 [1005 Metric]|[2362088](http://uk.farnell.com/webapp/wcs/stores/servlet/Search?st=2362088)|1|C21 2.2µF
|MC0402N180J500CT|MULTICOMP - SMD Multilayer Ceramic Capacitor, MC Series, 18 pF, Â± 5%, C0G / NP0, 50 V, 0402 [1005 Metric]|[1758947](http://uk.farnell.com/webapp/wcs/stores/servlet/Search?st=1758947)|2|C22, C23 18pF se880 y1 load
|06036D106MAT2A|AVX - SMD Multilayer Ceramic Capacitor, 10 ÂµF, Â± 20%, X5R, 6.3 V, 0603 [1608 Metric]|[1833804](http://uk.farnell.com/webapp/wcs/stores/servlet/Search?st=1833804)|3|C24, C25, C26 Solar input, Buck Out 10µF 0603
|C1005X5R0J475M050BC|TDK - SMD Multilayer Ceramic Capacitor, C Series, 4.7 ÂµF, Â± 20%, X5R, 6.3 V, 0402 [1005 Metric]|[2309027](http://uk.farnell.com/webapp/wcs/stores/servlet/Search?st=2309027)|6|C27, C28, C29, C30, C31, C32 Solar input, MPPT Output, Chg in, chg out, buck in 4.7µF
|MC0402B102J500CT|MULTICOMP - SMD Multilayer Ceramic Capacitor, MC Series, 1000 pF, Â± 5%, X7R, 50 V, 0402 [1005 Metric]|[2320765](http://uk.farnell.com/webapp/wcs/stores/servlet/Search?st=2320765)|3|C33, C34, C35 Mpp-set, vctrl, vcc-sup 1nF

----

### Misc

| Part | Description | Supplier | Quantity Required | Notes
| ---  | --- | --- | --- | ---
|M52-040023V0545|HARWIN - Board-To-Board Connector, Vertical, Archer M52 Series, Through Hole, Header, 5, 1.27 mm, Gold|[1099560](http://uk.farnell.com/webapp/wcs/stores/servlet/Search?st=1099560) [855-M52-040023V0545](http://uk.mouser.com/Search/Refine.aspx?N=1323043&Keyword=855-M52-040023V0545)|1|JTAG1
|742792731|WURTH ELEKTRONIK - FERRITE BEAD, 0.09OHM, 1.2A, 0402|[1961698](http://uk.farnell.com/webapp/wcs/stores/servlet/Search?st=1961698)|2|FB1, FB2
|CG0603MLC-05LE|BOURNS - ESD Protection Device, 25 V, 5 V, 0603, 2|[1828732](http://uk.farnell.com/webapp/wcs/stores/servlet/Search?st=1828732)|0|ESD1, ESD2
| | Antenna Wire | [ebay](http://www.ebay.co.uk/itm/Ernie-Ball-Custom-Gauge-Guitar-Single-Strings-Electric-or-Acoustic-Pack-6-13-/360959212478 ) | 1 | Ernie Ball .013

----

## Useful Hardware

| ID | Part Number | Description | Supplier | Order Code | Quantity
| --- | --- | --- | --- | --- | ---
|FFSD-05-D-06.00-01-N|SAMTEC - RIBBON CABLE, IDC, 152.4MM, GREY, 10WAY|[1667659](http://uk.farnell.com/webapp/wcs/stores/servlet/Search?st=1667659)|0|10way 1.27mm

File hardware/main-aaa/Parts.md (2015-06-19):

# Parts List

** Parts for HF Section not yet included **

----
### Active

| Part | Description | Supplier | Quantity Required | Notes
| ---  | --- | --- | --- | ---
|ATSAMD20E17A-MU|ATMEL - MCU, 32BIT, CORTEX-M0+, 48MHZ, QFN-32|[2361006](http://uk.farnell.com/webapp/wcs/stores/servlet/Search?st=2361006) [556-ATSAMD20E17A-MU](http://uk.mouser.com/Search/Refine.aspx?N=1323043&Keyword=556-ATSAMD20E17A-MU)|1|U1
|SI4468-A2A-IM|SILICON LABS - RF TRANSCEIVER, 0.142-1.05GHZ, HQFN-20|[2462639](http://uk.farnell.com/webapp/wcs/stores/servlet/Search?st=2462639) [634-SI4468-A2A-IM](http://uk.mouser.com/Search/Refine.aspx?N=1323043&Keyword=634-SI4468-A2A-IM)|1|U2
| UBLOX MAX-8C | GPS | [HAB Supplies](http://ava.upuaut.net/store/index.php?route=product/product&path=59_64&product_id=108) | 1 | U3
|SST25WF040BT-40I/NP|MICROCHIP - FLASH, 4MBIT, 40MHZ, USON-8|[2414758](http://uk.farnell.com/webapp/wcs/stores/servlet/Search?st=2414758) [579-25WF040BT-40I/NP](http://uk.mouser.com/Search/Refine.aspx?N=1323043&Keyword=579-25WF040BT-40I/NP)|1|U4 memory 4mbit
|X1G0041310008 TG-5006CJ-17H 16.369MHZ|EPSON - CRYSTAL, TCXO, TG-5006CJ-17H, 16.369 MHZ|[2405790](http://uk.farnell.com/webapp/wcs/stores/servlet/Search?st=2405790)|2|U5, U6 TCXO Si4xxx, SE880
|TPS3123J18DBVT|TEXAS INSTRUMENTS - IC, 1.62V SUPPLY MONITOR SOT-23-5|[1755607](http://uk.farnell.com/webapp/wcs/stores/servlet/Search?st=1755607) [595-TPS3123J8DBVT](http://uk.mouser.com/Search/Refine.aspx?N=1323043&Keyword=595-TPS3123J8DBVT)|1|U7 watchdog
|SN74LVC1G32DCKR|TEXAS INSTRUMENTS - IC, SINGLE 2 INPUT OR GATE, SMD|[1470880](http://uk.farnell.com/webapp/wcs/stores/servlet/Search?st=1470880) [595-SN74LVC1G32DCKR](http://uk.mouser.com/Search/Refine.aspx?N=1323043&Keyword=595-SN74LVC1G32DCKR)|1|U8 or-gate, watchdog subsystem
| SE880 | GPS | [Sequoia](http://www.sequoia.co.uk/product.php?id=1761) [Digikey](http://www.digikey.co.uk/product-detail/en/SE880GPSR22R003/943-1028-1-ND/5050348) | 1 | U9
|ADP1607ACPZN-R7|ANALOG DEVICES - BOOST, 0.8-3.3V, 2MHZ, 1.8-3.3V, 6LFCSP|[2254940](http://uk.farnell.com/webapp/wcs/stores/servlet/Search?st=2254940)|1|U10 Boost Reg
|ABS05-32.768KHZ-T|ABRACON - CRYSTAL, 32.768KHZ, 12.5PF, 1.6 X 1MM|[2467859](http://uk.farnell.com/webapp/wcs/stores/servlet/Search?st=2467859)|1|Y1 32.786kHz xtal Se880

----

### Passives

| Part | Description | Supplier | Quantity Required | Notes
| ---  | --- | --- | --- | ---
|CVH252009-3R3M|BOURNS - INDUCTOR, POWER, 20%, 3.3UH|[2118125](http://uk.farnell.com/webapp/wcs/stores/servlet/Search?st=2118125)|1|L1 Boost
|0402AF-221XJLU|COILCRAFT - INDUCTOR, RF, 220NH, 5%,1.15GHZ, SMD|[2285640](http://uk.farnell.com/webapp/wcs/stores/servlet/Search?st=2285640)|1|L2 220nH radio
|LQG15HN56NJ02D|MURATA - INDUCTOR, 0402 CASE, 56NHÂ±5%|[1343091](http://uk.farnell.com/webapp/wcs/stores/servlet/Search?st=1343091)|1|L3 56nH rf filter
|L-07C18NJV6T|JOHANSON TECHNOLOGY - INDUCTOR RF, 0402, 18NH, 5%|[1865775](http://uk.farnell.com/webapp/wcs/stores/servlet/Search?st=1865775)|1|L4, L5 18nH rf filter
| L6, L7 | DNP ||| si4xxx rx
|MC00625W0402110K|MULTICOMP - SMD Current Sense Resistors, MC Series, 10 kohm, 62.5 mW, Â± 1%, 50 V, 0402 [1005 Metric]|[1358069](http://uk.farnell.com/webapp/wcs/stores/servlet/Search?st=1358069)|4|R1, R4, R5, R6 10k
|CRG0402F100K|TE CONNECTIVITY - Surface Mount Thick Film Resistor, CRG Series, 100 kohm, 63 mW, Â± 1%, 50 V, 0402 [1005 Metric]|[2331442](http://uk.farnell.com/webapp/wcs/stores/servlet/Search?st=2331442)|3|R2, R9, R10 100k
|CRG0402F240K|TE CONNECTIVITY - Surface Mount Thick Film Resistor, CRG Series, 240 kohm, 63 mW, Â± 1%, 50 V, 0402 [1005 Metric]|[2331491](http://uk.farnell.com/webapp/wcs/stores/servlet/Search?st=2331491)|1|R3 240k
|GRM1555C1H8R2CA01D|MURATA - Multilayer Ceramic Capacitor, GRM Series, 8.2 pF, Â± 0.25pF, C0G / NP0, 50 V|[1828874](http://uk.farnell.com/webapp/wcs/stores/servlet/Search?st=1828874)|2|C1, C3 8.2pF
|MC0402N150J500CT|MULTICOMP - Multilayer Ceramic Capacitor, MC Series, 15 pF, Â± 5%, C0G / NP0, 50 V, 0402 [1005 Metric]|[1758945](http://uk.farnell.com/webapp/wcs/stores/servlet/Search?st=1758945)|3|C2, C4, C7 15pF
| C5, C6 | DNP ||| si4xxx rx
|MC0402N101J500CT|MULTICOMP - Multilayer Ceramic Capacitor, MC Series, 100 pF, Â± 5%, C0G / NP0, 50 V, 0402 [1005 Metric]|[1758969](http://uk.farnell.com/webapp/wcs/stores/servlet/Search?st=1758969)|3|C8, C9, C10 100pF
|MC0402X104K100CT|MULTICOMP - Multilayer Ceramic Capacitor, MC Series, 0.1 ÂµF, Â± 10%, X5R, 10 V, 0402 [1005 Metric]|[1759380](http://uk.farnell.com/webapp/wcs/stores/servlet/Search?st=1759380)|10|C11, C12, C13, C14, C15, C16, C17, C18, C19, C20 100nF
|GRM155R60J225ME15D|MURATA - Multilayer Ceramic Capacitor, GRM Series, 2.2 ÂµF, Â± 20%, X5R, 6.3 V, 0402 [1005 Metric]|[2362088](http://uk.farnell.com/webapp/wcs/stores/servlet/Search?st=2362088)|1|C21 2.2µF
|MC0402N180J500CT|MULTICOMP - Multilayer Ceramic Capacitor, MC Series, 18 pF, Â± 5%, C0G / NP0, 50 V, 0402 [1005 Metric]|[1758947](http://uk.farnell.com/webapp/wcs/stores/servlet/Search?st=1758947)|2|C22, C23 18pF se880 y1 load
|06036D106MAT2A|AVX - Multilayer Ceramic Capacitor, 10 ÂµF, Â± 20%, X5R, 6.3 V, 0603 [1608 Metric]|[1833804](http://uk.farnell.com/webapp/wcs/stores/servlet/Search?st=1833804)|2|C24, C25 10µF 0603 boost

----

### Misc

| Part | Description | Supplier | Quantity Required | Notes
| ---  | --- | --- | --- | ---
|M52-040023V0545|HARWIN - HEADER, THT, VERTICAL, 1.27MM, 5WAY|[1099560](http://uk.farnell.com/webapp/wcs/stores/servlet/Search?st=1099560) [855-M52-040023V0545](http://uk.mouser.com/Search/Refine.aspx?N=1323043&Keyword=855-M52-040023V0545)|1|JTAG1
|742792731|WURTH ELEKTRONIK - FERRITE BEAD, 0.09OHM, 1.2A, 0402|[1961698](http://uk.farnell.com/webapp/wcs/stores/servlet/Search?st=1961698)|2|FB1, FB2
|CG0603MLC-05LE|BOURNS - ESD SUPPRESSOR, 0603, 5V, 0.5PF|[1828732](http://uk.farnell.com/webapp/wcs/stores/servlet/Search?st=1828732)|0|ESD1, ESD2
| | Antenna Wire | [ebay](http://www.ebay.co.uk/itm/Ernie-Ball-Custom-Gauge-Guitar-Single-Strings-Electric-or-Acoustic-Pack-6-13-/360959212478 ) | 1 | Ernie Ball .013

----

## Useful Hardware

| ID | Part Number | Description | Supplier | Order Code | Quantity
| --- | --- | --- | --- | --- | ---
|FFSD-05-D-06.00-01-N|SAMTEC - RIBBON CABLE, IDC, 152.4MM, GREY, 10WAY|[1667659](http://uk.farnell.com/webapp/wcs/stores/servlet/Search?st=1667659)|0|10way 1.27mm

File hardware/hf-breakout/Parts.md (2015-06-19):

# Parts List

----
### Active

| Part | Description | Supplier | Quantity Required | Notes
| ---  | --- | --- | --- | ---
|ATSAMD20E17A-MU|ATMEL - MCU, 32BIT, CORTEX-M0+, 48MHZ, QFN-32|[2361006](http://uk.farnell.com/webapp/wcs/stores/servlet/Search?st=2361006) [556-ATSAMD20E17A-MU](http://uk.mouser.com/Search/Refine.aspx?N=1323043&Keyword=556-ATSAMD20E17A-MU)|1|U1
|SI5356A-B-GM|SILICON LABS - CLOCK GENERATOR, 200MHZ, QFN-24|[2421797](http://uk.farnell.com/webapp/wcs/stores/servlet/Search?st=2421797) [634-SI5356A-B-GM](http://uk.mouser.com/Search/Refine.aspx?N=1323043&Keyword=634-SI5356A-B-GM)|1|U2 HF Gen Si5356B
|AD8354ACPZ-REEL7|ANALOG DEVICES - RF/IF AMP, 19.5DB, 1MHZ-2.7GHZ, LFCSP-8|[2377134](http://uk.farnell.com/webapp/wcs/stores/servlet/Search?st=2377134) [584-AD8354ACPZ-R7](http://uk.mouser.com/Search/Refine.aspx?N=1323043&Keyword=584-AD8354ACPZ-R7)|1|U3 RF Amplifier
|X1G0041310008 TG-5006CJ-17H 16.369MHZ|EPSON - CRYSTAL, TCXO, TG-5006CJ-17H, 16.369 MHZ|[2405790](http://uk.farnell.com/webapp/wcs/stores/servlet/Search?st=2405790)|1|U6 TCXO
|TLV70018DCKT|TEXAS INSTRUMENTS - IC, LDO, 200MA, 1.8V, 5SC70|[1778221](http://uk.farnell.com/webapp/wcs/stores/servlet/Search?st=1778221) [595-TLV70018DCKT](http://uk.mouser.com/Search/Refine.aspx?N=1323043&Keyword=595-TLV70018DCKT)|1|U4 1.8V reg

----

### Passives

| Part | Description | Supplier | Quantity Required | Notes
| ---  | --- | --- | --- | ---
|0402AF-101XJLU|COILCRAFT - INDUCTOR, RF, 100NH, 5%, 1.4GHZ, SMD|[2285636](http://uk.farnell.com/webapp/wcs/stores/servlet/Search?st=2285636)|1|L1 100nH wirewound ferrite
|CRGH0603J10K|TE CONNECTIVITY - Surface Mount Thick Film Resistor, CRG Series, 10 kohm, 200 mW, Â± 5%, 50 V, 0603 [1608 Metric]|[2331740](http://uk.farnell.com/webapp/wcs/stores/servlet/Search?st=2331740)|4|R1, R2, R3, R4 10kΩ
|CRGH0603J15K|TE CONNECTIVITY - Surface Mount Thick Film Resistor, CRG Series, 15 kohm, 200 mW, Â± 5%, 50 V, 0603 [1608 Metric]|[2331742](http://uk.farnell.com/webapp/wcs/stores/servlet/Search?st=2331742)|1|R5 15kΩ
|CRGH0603J220R|TE CONNECTIVITY - Surface Mount Thick Film Resistor, CRG Series, 220 ohm, 200 mW, Â± 5%, 50 V, 0603 [1608 Metric]|[2331717](http://uk.farnell.com/webapp/wcs/stores/servlet/Search?st=2331717)|1|R6 220Ω
|MC0402X104K100CT|MULTICOMP - Multilayer Ceramic Capacitor, MC Series, 0.1 ÂµF, Â± 10%, X5R, 10 V, 0402 [1005 Metric]|[1759380](http://uk.farnell.com/webapp/wcs/stores/servlet/Search?st=1759380)|9|C1, C2, C3, C4, C5, C6, C7, C8, C9 100nF
|MC0402N101J500CT|MULTICOMP - Multilayer Ceramic Capacitor, MC Series, 100 pF, Â± 5%, C0G / NP0, 50 V, 0402 [1005 Metric]|[1758969](http://uk.farnell.com/webapp/wcs/stores/servlet/Search?st=1758969)|1|C10 100pF
|C1005X5R0J105K050BB|TDK - Multilayer Ceramic Capacitor, C Series, 1 ÂµF, Â± 10%, X5R, 6.3 V, 0402 [1005 Metric]|[2346871](http://uk.farnell.com/webapp/wcs/stores/servlet/Search?st=2346871)|2|C11, C12 1µF

----

### Misc

| Part | Description | Supplier | Quantity Required | Notes
| ---  | --- | --- | --- | ---
|20021121-00010C4LF|FCI - CONNECTOR, HEADER, SMT, R/A, 1.27MM, 10P|[1865279](http://uk.farnell.com/webapp/wcs/stores/servlet/Search?st=1865279) [649-202112100010C4LF](http://uk.mouser.com/Search/Refine.aspx?N=1323043&Keyword=649-202112100010C4LF)|1|JTAG1
|742792731|WURTH ELEKTRONIK - FERRITE BEAD, 0.09OHM, 1.2A, 0402|[1961698](http://uk.farnell.com/webapp/wcs/stores/servlet/Search?st=1961698)|2|FB1, FB2

----

## Useful Hardware

| ID | Part Number | Description | Supplier | Order Code | Quantity
| --- | --- | --- | --- | --- | ---
|FFSD-05-D-06.00-01-N|SAMTEC - RIBBON CABLE, IDC, 152.4MM, GREY, 10WAY|[1667659](http://uk.farnell.com/webapp/wcs/stores/servlet/Search?st=1667659)|0|10way 1.27mm

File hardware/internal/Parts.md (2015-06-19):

# Parts List

** Parts for HF Section not yet included **

----
### Active

| Part | Description | Supplier | Quantity Required | Notes
| ---  | --- | --- | --- | ---
|ATSAMD20E17A-MU|ATMEL - MCU, 32BIT, CORTEX-M0+, 48MHZ, QFN-32|[2361006](http://uk.farnell.com/webapp/wcs/stores/servlet/Search?st=2361006) [556-ATSAMD20E17A-MU](http://uk.mouser.com/Search/Refine.aspx?N=1323043&Keyword=556-ATSAMD20E17A-MU)|1|U1
|SI4467-A2A-IM|SILICON LABS - RF TRANSCEIVER, 0.142-1.05GHZ, HQFN-20|[2462638](http://uk.farnell.com/webapp/wcs/stores/servlet/Search?st=2462638) [634-SI4467-A2A-IM](http://uk.mouser.com/Search/Refine.aspx?N=1323043&Keyword=634-SI4467-A2A-IM)|1|U2
|BMP180|Board Mount Pressure Sensors Digital Barometer 12uA, 300-1200hPa|[262-BMP180](http://uk.mouser.com/Search/Refine.aspx?N=1323043&Keyword=262-BMP180)|1|U3 pressure sensor
|7M-30.000MAAJ-T|TXC - XTAL, 30.000MHZ, 18PF, SMD, 3.2X2.5|[1842071](http://uk.farnell.com/webapp/wcs/stores/servlet/Search?st=1842071) [717-7M-30.000MAAJ-T](http://uk.mouser.com/Search/Refine.aspx?N=1323043&Keyword=717-7M-30.000MAAJ-T)|1|U4 30MHz xtal
|0433AT62A0020E|JOHANSON TECHNOLOGY - ANTENNA, AT62|[2148530](http://uk.farnell.com/webapp/wcs/stores/servlet/Search?st=2148530) [609-0433AT62A0020E](http://uk.mouser.com/Search/Refine.aspx?N=1323043&Keyword=609-0433AT62A0020E)|1|U5 434 chip antenna
|TPS3123J18DBVT|TEXAS INSTRUMENTS - IC, 1.62V SUPPLY MONITOR SOT-23-5|[1755607](http://uk.farnell.com/webapp/wcs/stores/servlet/Search?st=1755607) [595-TPS3123J8DBVT](http://uk.mouser.com/Search/Refine.aspx?N=1323043&Keyword=595-TPS3123J8DBVT)|1|U7 watchdog
|SN74LVC1G32DCKR|TEXAS INSTRUMENTS - IC, SINGLE 2 INPUT OR GATE, SMD|[1470880](http://uk.farnell.com/webapp/wcs/stores/servlet/Search?st=1470880) [595-SN74LVC1G32DCKR](http://uk.mouser.com/Search/Refine.aspx?N=1323043&Keyword=595-SN74LVC1G32DCKR)|1|U8 or-gate

----

### Passives

| Part | Description | Supplier | Quantity Required | Notes
| ---  | --- | --- | --- | ---
|0402AF-221XJLU|COILCRAFT - INDUCTOR, RF, 220NH, 5%,1.15GHZ, SMD|[2285640](http://uk.farnell.com/webapp/wcs/stores/servlet/Search?st=2285640)|1|L2 220nH radio
|LQG15HN56NJ02D|MURATA - INDUCTOR, 0402 CASE, 56NHÂ±5%|[1343091](http://uk.farnell.com/webapp/wcs/stores/servlet/Search?st=1343091)|1|L3 56nH filter
|L-07C18NJV6T|JOHANSON TECHNOLOGY - INDUCTOR RF, 0402, 18NH, 5%|[1865775](http://uk.farnell.com/webapp/wcs/stores/servlet/Search?st=1865775)|1|L4, L5 18nH filter
| L6, L7 | DNP ||| si4xxx rx
|MC00625W0402110K|MULTICOMP - SMD Current Sense Resistors, MC Series, 10 kohm, 62.5 mW, Â± 1%, 50 V, 0402 [1005 Metric]|[1358069](http://uk.farnell.com/webapp/wcs/stores/servlet/Search?st=1358069)|4|R1, R2, R3, R7 10k
|CRG0402F22K|TE CONNECTIVITY - Surface Mount Thick Film Resistor, CRG Series, 22 kohm, 63 mW, Â± 1%, 50 V, 0402 [1005 Metric]|[2331489](http://uk.farnell.com/webapp/wcs/stores/servlet/Search?st=2331489)|1|R8 22k
|GRM1555C1H8R2CA01D|MURATA - Multilayer Ceramic Capacitor, GRM Series, 8.2 pF, Â± 0.25pF, C0G / NP0, 50 V|[1828874](http://uk.farnell.com/webapp/wcs/stores/servlet/Search?st=1828874)|2|C1, C3 8.2pF
|MC0402N150J500CT|MULTICOMP - Multilayer Ceramic Capacitor, MC Series, 15 pF, Â± 5%, C0G / NP0, 50 V, 0402 [1005 Metric]|[1758945](http://uk.farnell.com/webapp/wcs/stores/servlet/Search?st=1758945)|5|C2, C4, C7, C9, C10 rf, xtal load 15pF
| C5, C6 | DNP ||| si4xxx rx
|MC0402N101J500CT|MULTICOMP - Multilayer Ceramic Capacitor, MC Series, 100 pF, Â± 5%, C0G / NP0, 50 V, 0402 [1005 Metric]|[1758969](http://uk.farnell.com/webapp/wcs/stores/servlet/Search?st=1758969)|1|C8 100pF
|MC0402X104K100CT|MULTICOMP - Multilayer Ceramic Capacitor, MC Series, 0.1 ÂµF, Â± 10%, X5R, 10 V, 0402 [1005 Metric]|[1759380](http://uk.farnell.com/webapp/wcs/stores/servlet/Search?st=1759380)|8|C11, C12, C15, C16, C17 100nF
|C1005X5R0J475M050BC|TDK - Multilayer Ceramic Capacitor, C Series, 4.7 ÂµF, Â± 20%, X5R, 6.3 V, 0402 [1005 Metric]|[2309027](http://uk.farnell.com/webapp/wcs/stores/servlet/Search?st=2309027)|1|C18 pressure sens 4.7µF

----

### Misc

| Part | Description | Supplier | Quantity Required | Notes
| ---  | --- | --- | --- | ---
|M52-040023V0545|HARWIN - HEADER, THT, VERTICAL, 1.27MM, 5WAY|[1099560](http://uk.farnell.com/webapp/wcs/stores/servlet/Search?st=1099560) [855-M52-040023V0545](http://uk.mouser.com/Search/Refine.aspx?N=1323043&Keyword=855-M52-040023V0545)|1|JTAG1
|CR-2032/BN|PANASONIC ELECTRONIC COMPONENTS - Non-rechargeable Battery, Lithium Manganese Dioxide, 220 mAh, 3 V, 2032, Pressure Contact|[5219590](http://uk.farnell.com/webapp/wcs/stores/servlet/Search?st=5219590)|1|2032 coin cell LMnO2 220mAh
|BC-2001|MULTICOMP - RETAINER CLIP, 20MM, SMT|[2064713](http://uk.farnell.com/webapp/wcs/stores/servlet/Search?st=2064713)|1|J2 Coin Cell Connector 2032
|BLM15BB100SN1D|MURATA - FERRITE BEAD, 0.1OHM, 300MA, 0402|[1515765](http://uk.farnell.com/webapp/wcs/stores/servlet/Search?st=1515765)|1|FB1

----

## Useful Hardware

| ID | Part Number | Description | Supplier | Order Code | Quantity
| --- | --- | --- | --- | --- | ---
|FFSD-05-D-06.00-01-N|SAMTEC - RIBBON CABLE, IDC, 152.4MM, GREY, 10WAY|[1667659](http://uk.farnell.com/webapp/wcs/stores/servlet/Search?st=1667659)|0|10way 1.27mm

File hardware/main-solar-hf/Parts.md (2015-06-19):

# Parts List

** Parts for HF Section not yet included **

----
### Active

| Part | Description | Supplier | Quantity Required | Notes
| ---  | --- | --- | --- | ---
|ATSAMD20E17A-MU|ATMEL - MCU, 32BIT, CORTEX-M0+, 48MHZ, QFN-32|[2361006](http://uk.farnell.com/webapp/wcs/stores/servlet/Search?st=2361006) [556-ATSAMD20E17A-MU](http://uk.mouser.com/Search/Refine.aspx?N=1323043&Keyword=556-ATSAMD20E17A-MU)|1|U1
|SI4060-B1B-FM|SILICON LABS - RF TRANSMITTER, 142MHZ-1.05GHZ, QFN-20|[2414373](http://uk.farnell.com/webapp/wcs/stores/servlet/Search?st=2414373) [634-SI4060-B1B-FM](http://uk.mouser.com/Search/Refine.aspx?N=1323043&Keyword=634-SI4060-B1B-FM)|1|U2
|SI4060-B1B-FM|SILICON LABS - RF TRANSMITTER, 142MHZ-1.05GHZ, QFN-20|[2414373](http://uk.farnell.com/webapp/wcs/stores/servlet/Search?st=2414373) [634-SI4063-B1B-FM](http://uk.mouser.com/Search/Refine.aspx?N=1323043&Keyword=634-SI4063-B1B-FM)|1|U2
| UBLOX MAX-8C | GPS | [HAB Supplies]() | 1 | U3
|S25FS128SAGNFI101|SPANSION - IC, MEMORY, FLASH, 128MBIT, 1.8V, 8WSON|[2367709](http://uk.farnell.com/webapp/wcs/stores/servlet/Search?st=2367709) [797-25FS128SAGNFI101](http://uk.mouser.com/Search/Refine.aspx?N=1323043&Keyword=797-25FS128SAGNFI101)|0|U4 memory
|X1G0041310008 TG-5006CJ-17H 16.369MHZ|EPSON - CRYSTAL, TCXO, TG-5006CJ-17H, 16.369 MHZ|[2405790](http://uk.farnell.com/webapp/wcs/stores/servlet/Search?st=2405790)|1|U5 TCXO
| U6 | DNP
|TPS3123J18DBVT|TEXAS INSTRUMENTS - IC, 1.62V SUPPLY MONITOR SOT-23-5|[1755607](http://uk.farnell.com/webapp/wcs/stores/servlet/Search?st=1755607) [595-TPS3123J8DBVT](http://uk.mouser.com/Search/Refine.aspx?N=1323043&Keyword=595-TPS3123J8DBVT)|1|U7 watchdog
|SN74LVC1G32DCKR|TEXAS INSTRUMENTS - IC, SINGLE 2 INPUT OR GATE, SMD|[1470880](http://uk.farnell.com/webapp/wcs/stores/servlet/Search?st=1470880) [595-SN74LVC1G32DCKR](http://uk.mouser.com/Search/Refine.aspx?N=1323043&Keyword=595-SN74LVC1G32DCKR)|1|U8 or-gate

----

### Passives

| Part | Description | Supplier | Quantity Required | Notes
| ---  | --- | --- | --- | ---
|0402AF-221XJLU|COILCRAFT - INDUCTOR, RF, 220NH, 5%,1.15GHZ, SMD|[2285640](http://uk.farnell.com/webapp/wcs/stores/servlet/Search?st=2285640)|1|L2 220nH radio
|LQG15HN56NJ02D|MURATA - INDUCTOR, 0402 CASE, 56NHÂ±5%|[1343091](http://uk.farnell.com/webapp/wcs/stores/servlet/Search?st=1343091)|1|L3 56nH filter
|L-07C18NJV6T|JOHANSON TECHNOLOGY - INDUCTOR RF, 0402, 18NH, 5%|[1865775](http://uk.farnell.com/webapp/wcs/stores/servlet/Search?st=1865775)|1|L4, L5 18nH filter
| L6 | DNP
|MC00625W0402110K|MULTICOMP - SMD Current Sense Resistors, MC Series, 10 kohm, 62.5 mW, Â± 1%, 50 V, 0402 [1005 Metric]|[1358069](http://uk.farnell.com/webapp/wcs/stores/servlet/Search?st=1358069)|4|R1, R2, R3, R7 10k
| R4, R5, R6 | DNP
|CRG0402F22K|TE CONNECTIVITY - Surface Mount Thick Film Resistor, CRG Series, 22 kohm, 63 mW, Â± 1%, 50 V, 0402 [1005 Metric]|[2331489](http://uk.farnell.com/webapp/wcs/stores/servlet/Search?st=2331489)|1|R8 22k
|CRG0402F100K|TE CONNECTIVITY - Surface Mount Thick Film Resistor, CRG Series, 100 kohm, 63 mW, Â± 1%, 50 V, 0402 [1005 Metric]|[2331442](http://uk.farnell.com/webapp/wcs/stores/servlet/Search?st=2331442)|2|R9, R10 100k
|GRM1555C1H8R2CA01D|MURATA - Multilayer Ceramic Capacitor, GRM Series, 8.2 pF, Â± 0.25pF, C0G / NP0, 50 V|[1828874](http://uk.farnell.com/webapp/wcs/stores/servlet/Search?st=1828874)|2|C1, C3 8.2pF
|MC0402N150J500CT|MULTICOMP - Multilayer Ceramic Capacitor, MC Series, 15 pF, Â± 5%, C0G / NP0, 50 V, 0402 [1005 Metric]|[1758945](http://uk.farnell.com/webapp/wcs/stores/servlet/Search?st=1758945)|3|C2, C4, C7 15pF
| C5, C6 | DNP
|MC0402N101J500CT|MULTICOMP - Multilayer Ceramic Capacitor, MC Series, 100 pF, Â± 5%, C0G / NP0, 50 V, 0402 [1005 Metric]|[1758969](http://uk.farnell.com/webapp/wcs/stores/servlet/Search?st=1758969)|3|C8, C9, C10 100pF
|MC0402X104K100CT|MULTICOMP - Multilayer Ceramic Capacitor, MC Series, 0.1 ÂµF, Â± 10%, X5R, 10 V, 0402 [1005 Metric]|[1759380](http://uk.farnell.com/webapp/wcs/stores/servlet/Search?st=1759380)|8|C11, C12, C13, C14, C15, C16, C17, C18 100nF
| C19, C20 | DNP
|GRM155R60J225ME15D|MURATA - Multilayer Ceramic Capacitor, GRM Series, 2.2 ÂµF, Â± 20%, X5R, 6.3 V, 0402 [1005 Metric]|[2362088](http://uk.farnell.com/webapp/wcs/stores/servlet/Search?st=2362088)|1|C21 2.2µF
| C22, C23 | DNP

----

### Misc

| Part | Description | Supplier | Quantity Required | Notes
| ---  | --- | --- | --- | ---
|20021121-00010C4LF|FCI - CONNECTOR, HEADER, SMT, R/A, 1.27MM, 10P|[1865279](http://uk.farnell.com/webapp/wcs/stores/servlet/Search?st=1865279) [649-202112100010C4LF](http://uk.mouser.com/Search/Refine.aspx?N=1323043&Keyword=649-202112100010C4LF)|1|JTAG1
|20021111-00008T4LF|FCI - HEADER, VERT, 1.27MM, THT, 8WAY|[1865284](http://uk.farnell.com/webapp/wcs/stores/servlet/Search?st=1865284)|1|Interconnect Header
|BLM15BB100SN1D|MURATA - FERRITE BEAD, 0.1OHM, 300MA, 0402|[1515765](http://uk.farnell.com/webapp/wcs/stores/servlet/Search?st=1515765)|2|FB1, FB2
|CG0603MLC-05LE|BOURNS - ESD SUPPRESSOR, 0603, 5V, 0.5PF|[1828732](http://uk.farnell.com/webapp/wcs/stores/servlet/Search?st=1828732)|2|ESD1, ESD2
| | Antenna Wire | [ebay](http://www.ebay.co.uk/itm/Ernie-Ball-Custom-Gauge-Guitar-Single-Strings-Electric-or-Acoustic-Pack-6-13-/360959212478 ) | 1 | Ernie Ball .013

----
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

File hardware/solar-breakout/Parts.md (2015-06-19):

# Parts List

---

## Actives

| Part | Description | Supplier | Quantity Required | Notes
| ---  | --- | --- | --- | ---
|SPV1040T|Voltage Regulators - Switching Regulators Hi efficiency solar battery charger|[511-SPV1040T](http://uk.mouser.com/Search/Refine.aspx?N=1323043&Keyword=511-SPV1040T)|2|MPPT U1, U2
|LTC4054LES5-4.2#PBF|LINEAR TECHNOLOGY - CHARGER, BATTERY, LI-ION, 0.15A, 5SOT23|[2102610](http://uk.farnell.com/webapp/wcs/stores/servlet/Search?st=2102610)|1|Li-ion charge controller U3
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

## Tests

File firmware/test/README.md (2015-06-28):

## Verification

#### Setup

```
sudo apt-get install python-pip
sudo pip install colorama
```

#### Usage

Something like this.

`> /dev/null arm-none-eabi-gdb -q -x tools/tests.py `

You need to have your debugger configured in config.mk and possibly
also have gdbscript-custom. The test driver just issues an `attach 1`
command after gdb startup and expects that to work.

##### From the makefile

From the main firmware makefile you can just run

```
make test
```

to run all tests, or

```
make test tc=<tc name>
```

to run a specific test case. To get extra debug info

```
make test tc=<tc name> tc-gdb-info=1
```

#### Operation

Initially `tests.py` loads the latest binary, and runs `Reset_Handler`
until the top of `main`. It then jumps to `tc_main` instead.

While stopped in `tc_main` a pointer to the test case is set. The
program is then run, and one loop of `tc_main` runs the test case.

#### Writing a new test case

```
From this directory you can just run 'make name=<new_name>'
```

* Choose a testcase name `[tc-name]`
* Create `tc/[tc-name].py` and `tc/[tc_name].h`. Use a pre-existing test case as a template.
* Add `#include [tc-name].h` to the section at the top of `tmain.c`

You'll need to fill in the `/* Parameters In */` and `/* Results Out
*/` structures in `tc/[tc-name].h`

`tc/[tc-name].py` must contain a class called `[tc-name]_tc` that
defines `get_test` and `is_correct` methods.

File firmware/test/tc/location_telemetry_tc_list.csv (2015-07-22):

# name | ? | lat | lon
# Permitted
UK | 1 | 52 | -1
UK | 1 | 52 | 0
UK | 1 | 52 | 1
Wales | 1 | 52 | -4
Lewis | 1 | 58 | -6.5
NI | 1 | 54.5 | -6.5
France | 1 | 49 | 2
Portugal | 1 | 40 | -8
Italy | 1 | 43 | 12
Romania | 1 | 46 | 24
Sweden | 1 | 58 | 12
Stockholm | 1 | 59.3 | 18
Malmo | 1 | 55.6 | 13
Copenhagen | 1 | 55.7 | 12.5
Amsterdam | 1 | 52.4 | 5.7
Germany | 1 | 52 | 9
Poland | 1 | 51 | 20
Russia | 1 | 55 | 37
Mongolia | 1 | 48 | 107
Vladivostok | 1 | 43 | 132
Armenia | 1 | 40 | 44
Africa | 1 | 9 | 2
LA | 1 | 34 | -118
New York | 1 | 41 | -74
Canada | 1 | 44 | -76
South Korea | 1 | 37 | 128
Japan | 1 | 36 | 140
Thailand | 1 | 14 | 100
# Not permitted
West China | 0 | 39 | 80
Beijing | 0 | 40 | 116
Hong Kong | 0 | 22.4 | 114.1
Yemen | 0 | 15 | 44
NK | 0 | 39 | 126

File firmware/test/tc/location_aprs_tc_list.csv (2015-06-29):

# name | frequency | lat | lon
# not allowed
UK | 0 | 52 | -1
UK | 0 | 52 | 0
UK | 0 | 52 | 1
Wales | 0 | 52 | -4
Lewis | 0 | 58 | -6.5
NI | 0 | 54.5 | -6.5
France | 0 | 49 | 2
Portugal | 0 | 40 | -8
Italy | 0 | 43 | 12
Romania | 0 | 46 | 24
Sweden | 0 | 58 | 12
Stockholm | 0 | 59.3 | 18
Malmo | 0 | 55.6 | 13
Yemen | 0 | 15 | 44
NK | 0 | 39 | 126
# 144.8
Copenhagen | 144.8 | 55.7 | 12.5
Amsterdam | 144.8 | 52.4 | 5.7
Germany | 144.8 | 52 | 9
Poland | 144.8 | 51 | 20
Russia | 144.8 | 55 | 37
Mongolia | 144.8 | 48 | 107
Vladivostok | 144.8 | 43 | 132
Armenia | 144.8 | 40 | 44
Africa | 144.8 | 9 | 2
# 144.39
LA | 144.39 | 34 | -118
New York | 144.39 | 41 | -74
Canada | 144.39 | 44 | -76
# 144.62
South Korea | 144.62 | 37 | 128
# 144.64
West China | 144.64 | 39 | 80
Beijing | 144.64 | 40 | 116
Hong Kong | 144.64 | 22.4 | 114.1
# 144.66
Japan | 144.66 | 36 | 140
# 145.525
Thailand | 145.525 | 14 | 100

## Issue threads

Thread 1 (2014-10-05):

External watchdog prevents debug of Atmel SAM D20

richardeoin, 2014-10-05:
When the debugger is connected and the processor halts, the external watchdog repeatedly drives !RESET, which leads to a extended reset. This prevents the debugger from attaching.

**Fix:** Connect the !MR of the watchdog to the !RESET line of the ARM cortex debug connector
**Workaround:** Remove the watchdog while debugging

richardeoin, 2015-02-27:
Fixed in 0f63533

Closed 2015-02-27.

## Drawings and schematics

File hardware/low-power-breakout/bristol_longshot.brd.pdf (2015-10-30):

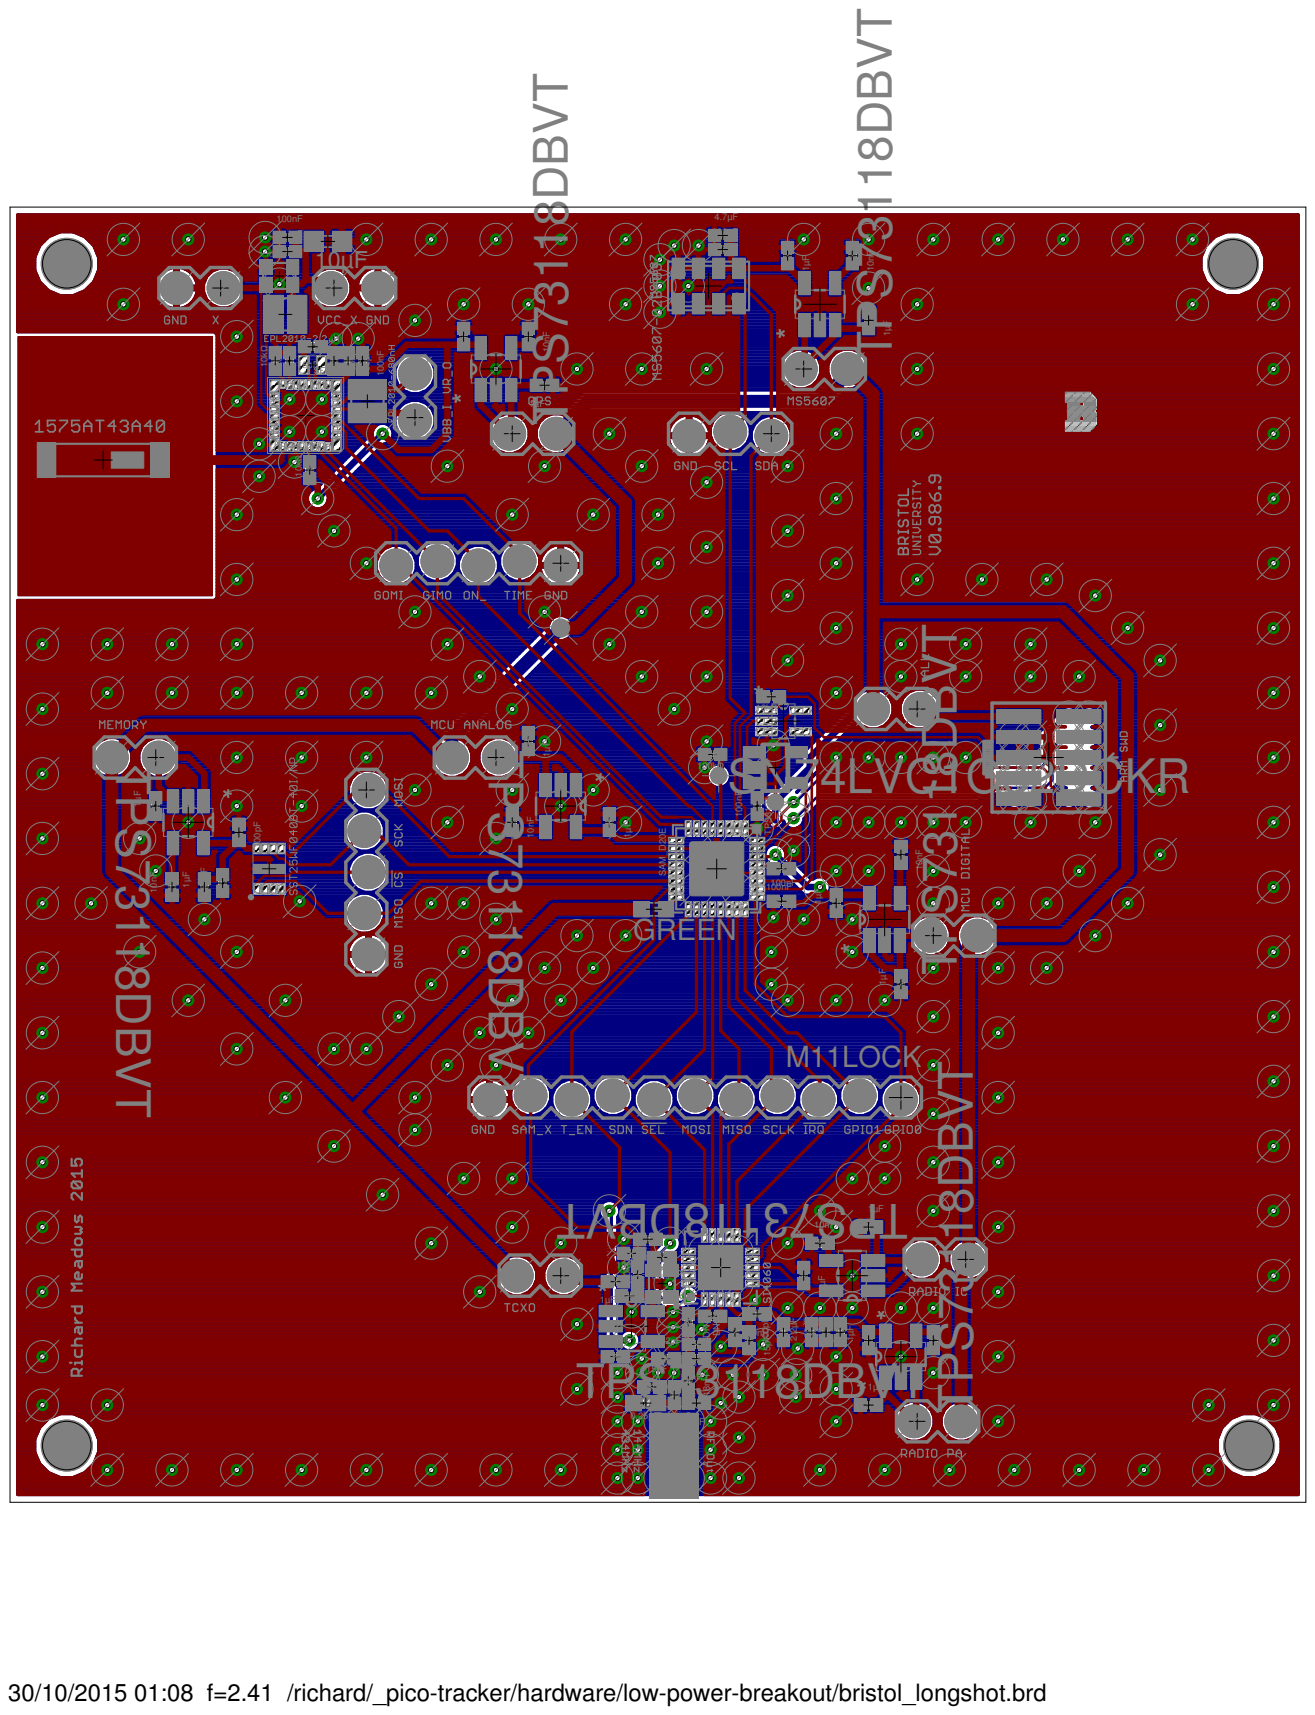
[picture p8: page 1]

TPS73118DBVT 15pF | 56nH

30/10/2015 01:08 f=2.41 /richard/_pico-tracker/hardware/low-power-breakout/bristol_longshot.brd

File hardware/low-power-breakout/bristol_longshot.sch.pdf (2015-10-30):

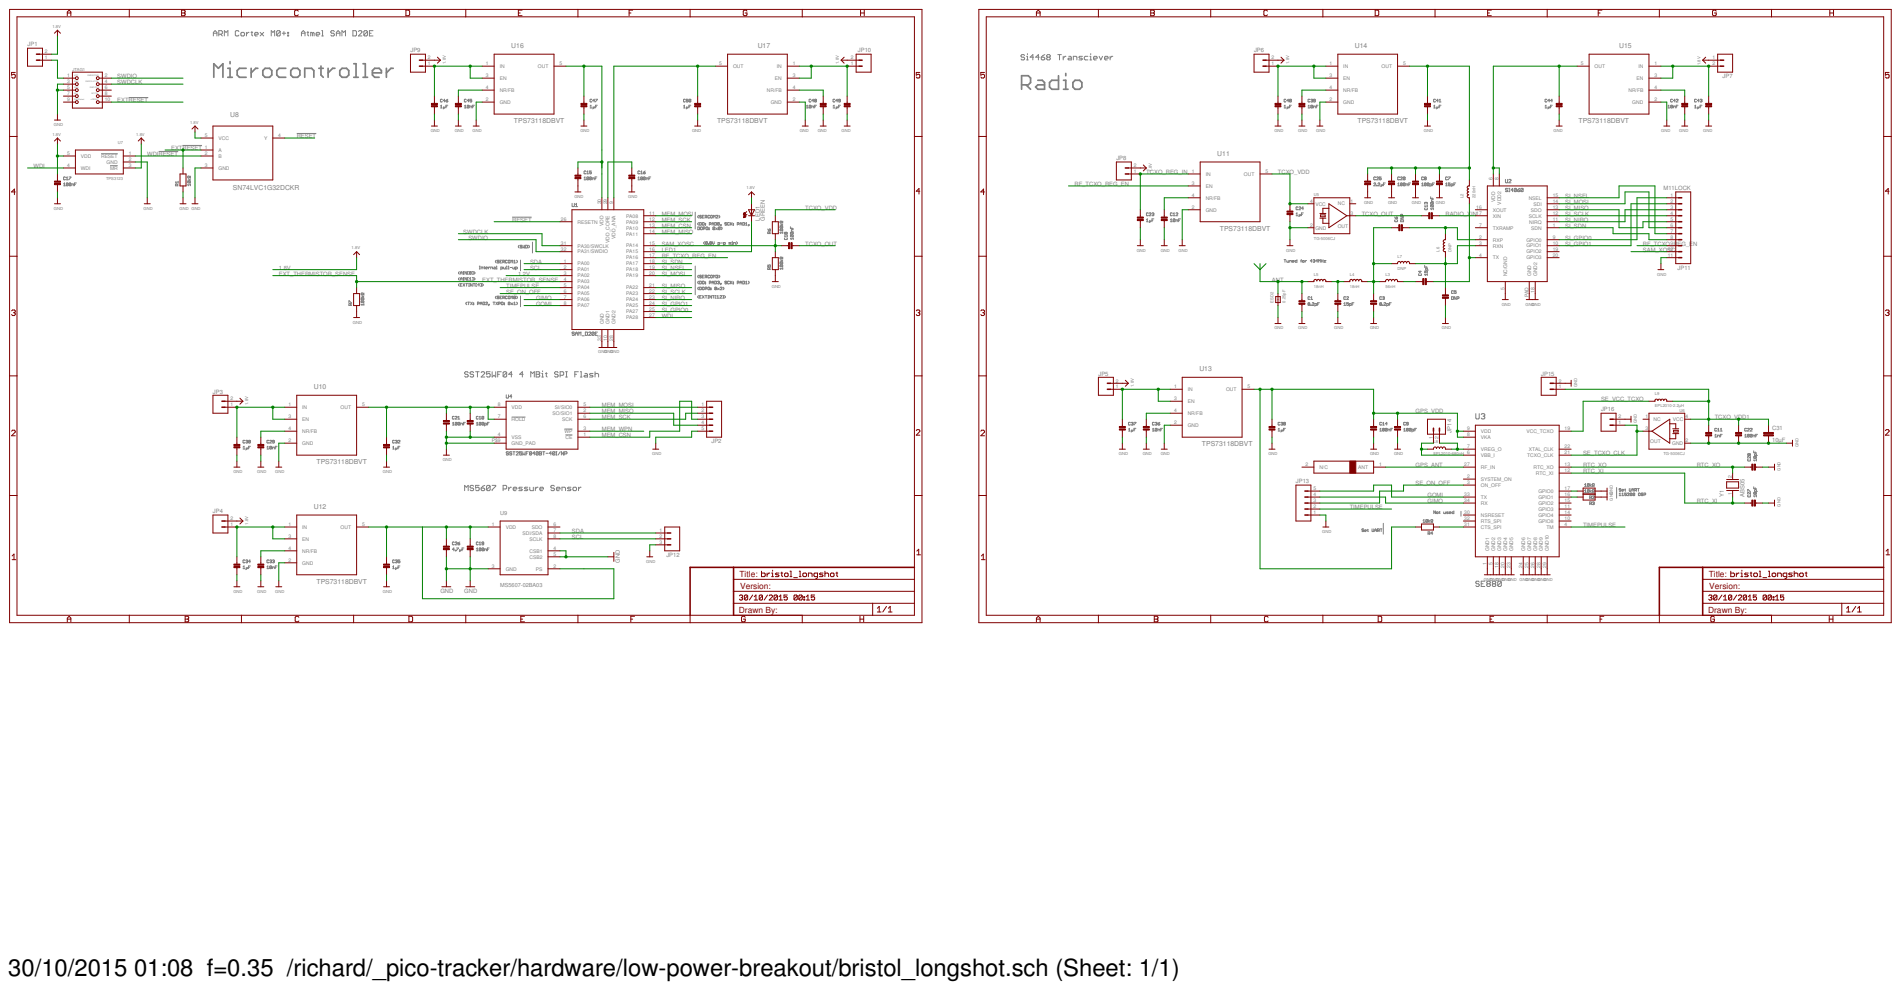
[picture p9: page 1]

nRESET NC/TDI SWO/TDO

30/10/2015 01:08 f=0.35 /richard/_pico-tracker/hardware/low-power-breakout/bristol_longshot.sch (Sheet: 1/1)

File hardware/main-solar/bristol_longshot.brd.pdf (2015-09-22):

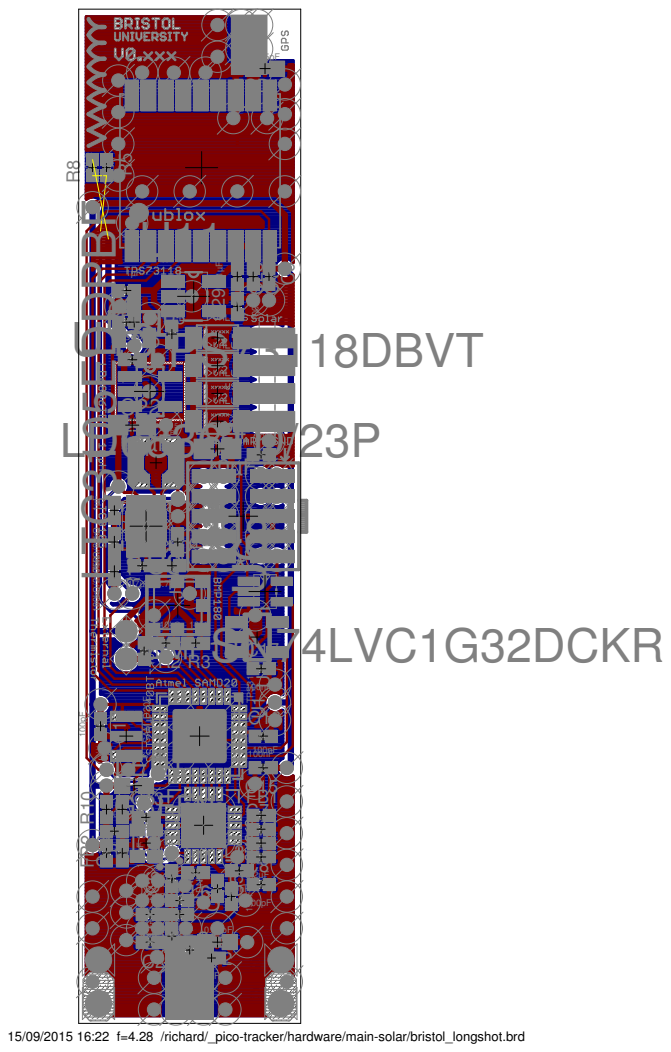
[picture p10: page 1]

L2
15pF

220nH
100pF

15/09/2015 16:22 f=4.28 /richard/_pico-tracker/hardware/main-solar/bristol_longshot.brd

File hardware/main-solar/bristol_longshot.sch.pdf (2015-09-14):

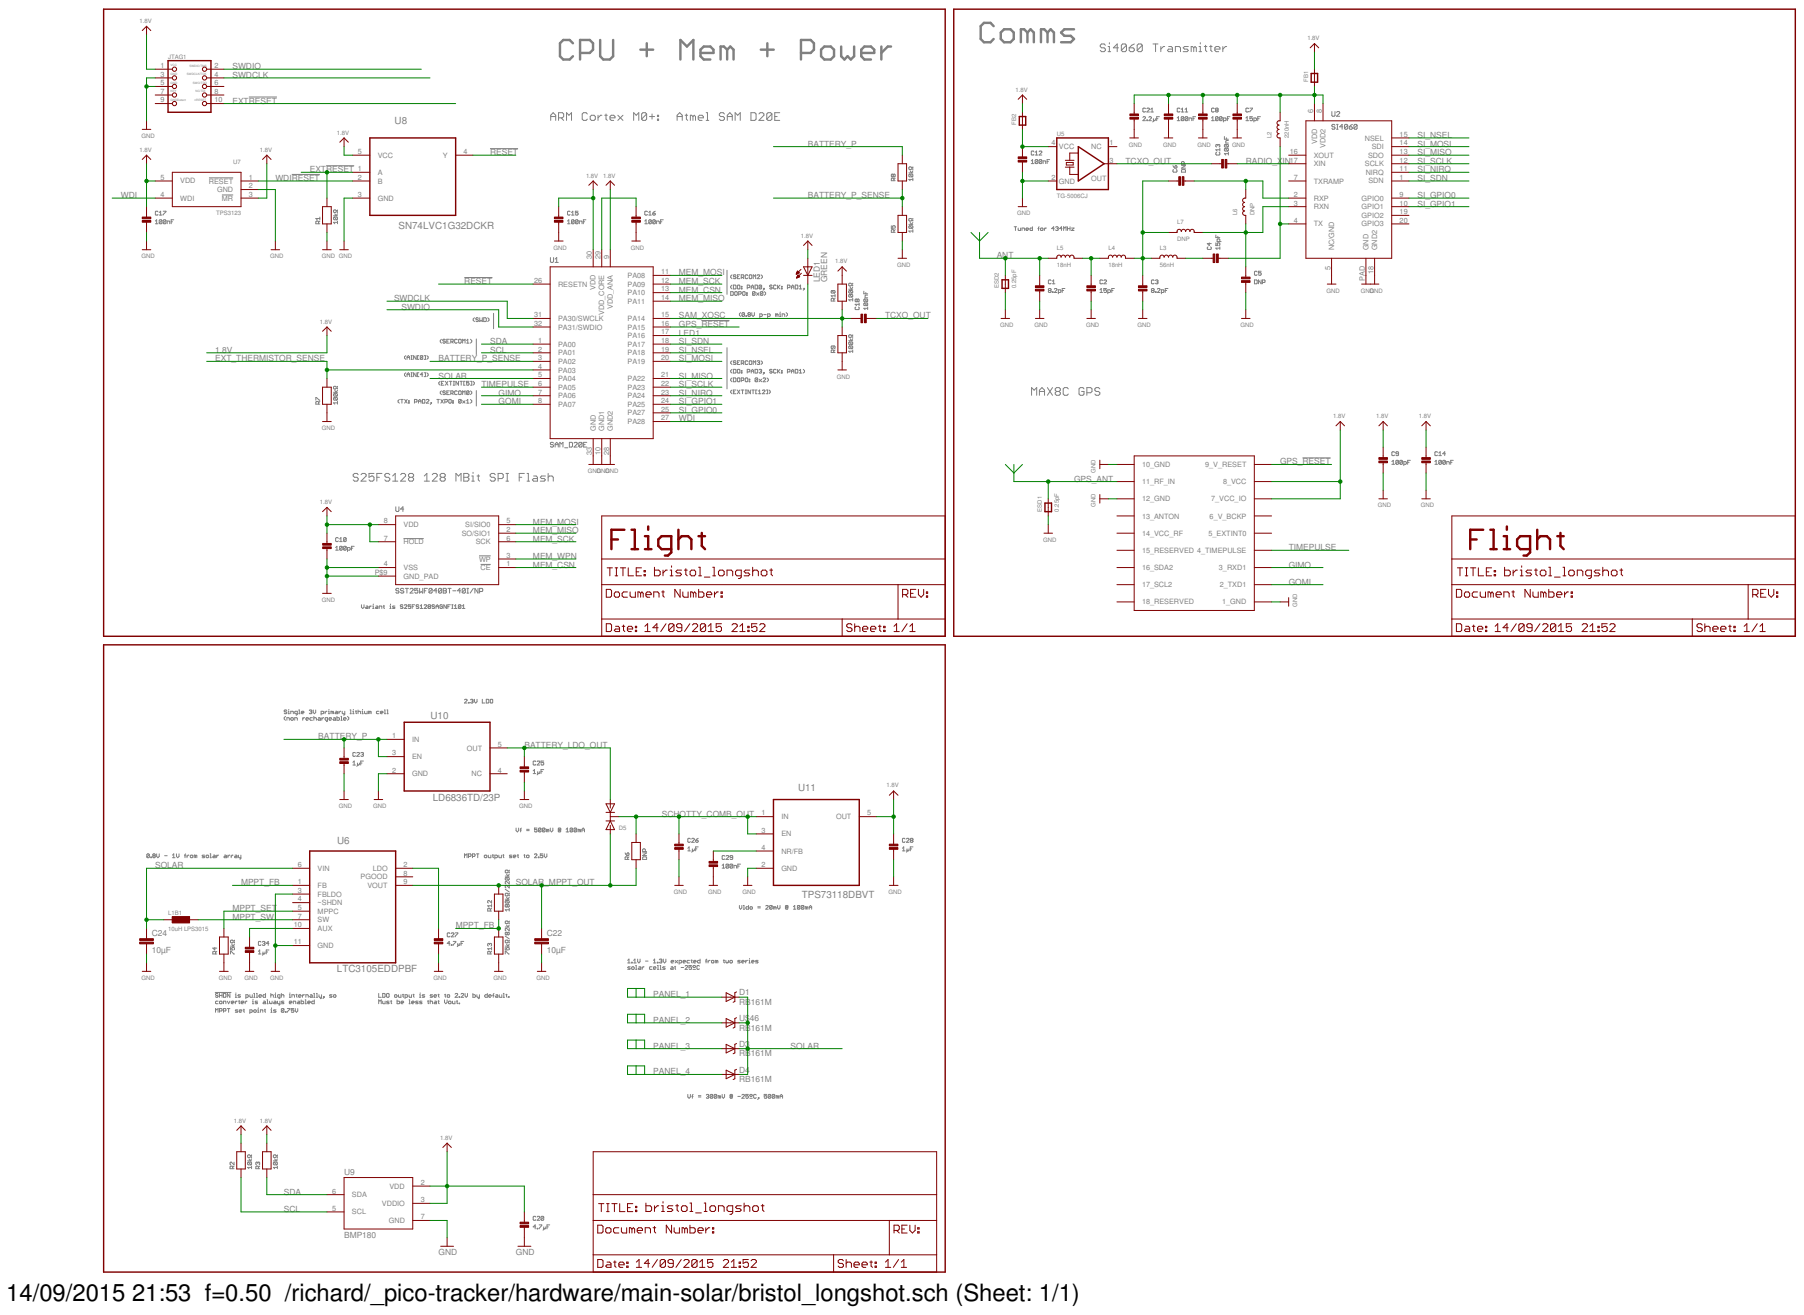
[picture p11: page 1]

nRESET NC/TDI SWO/TDO

14/09/2015 21:53 f=0.50 /richard/_pico-tracker/hardware/main-solar/bristol_longshot.sch (Sheet: 1/1)

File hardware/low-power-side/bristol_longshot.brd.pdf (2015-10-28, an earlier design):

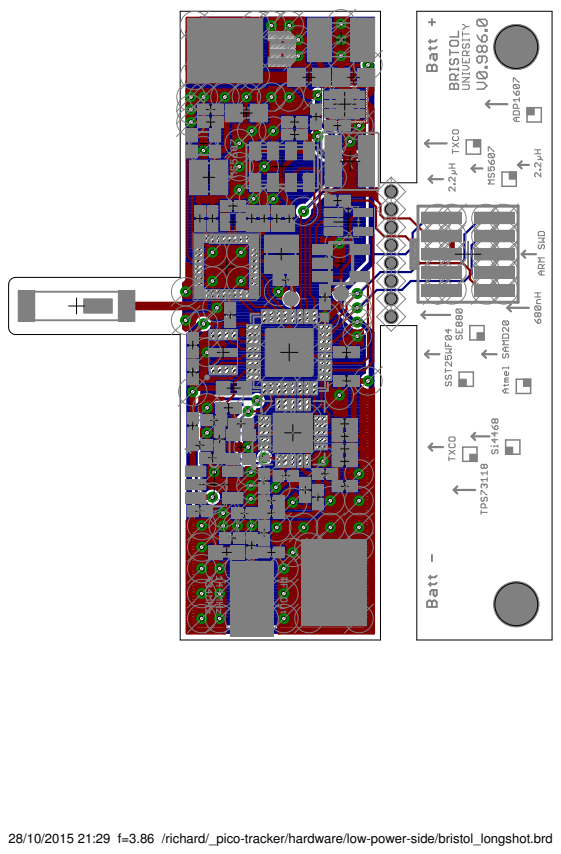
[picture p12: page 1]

28/10/2015 21:29 f=3.86 /richard/_pico-tracker/hardware/low-power-side/bristol_longshot.brd

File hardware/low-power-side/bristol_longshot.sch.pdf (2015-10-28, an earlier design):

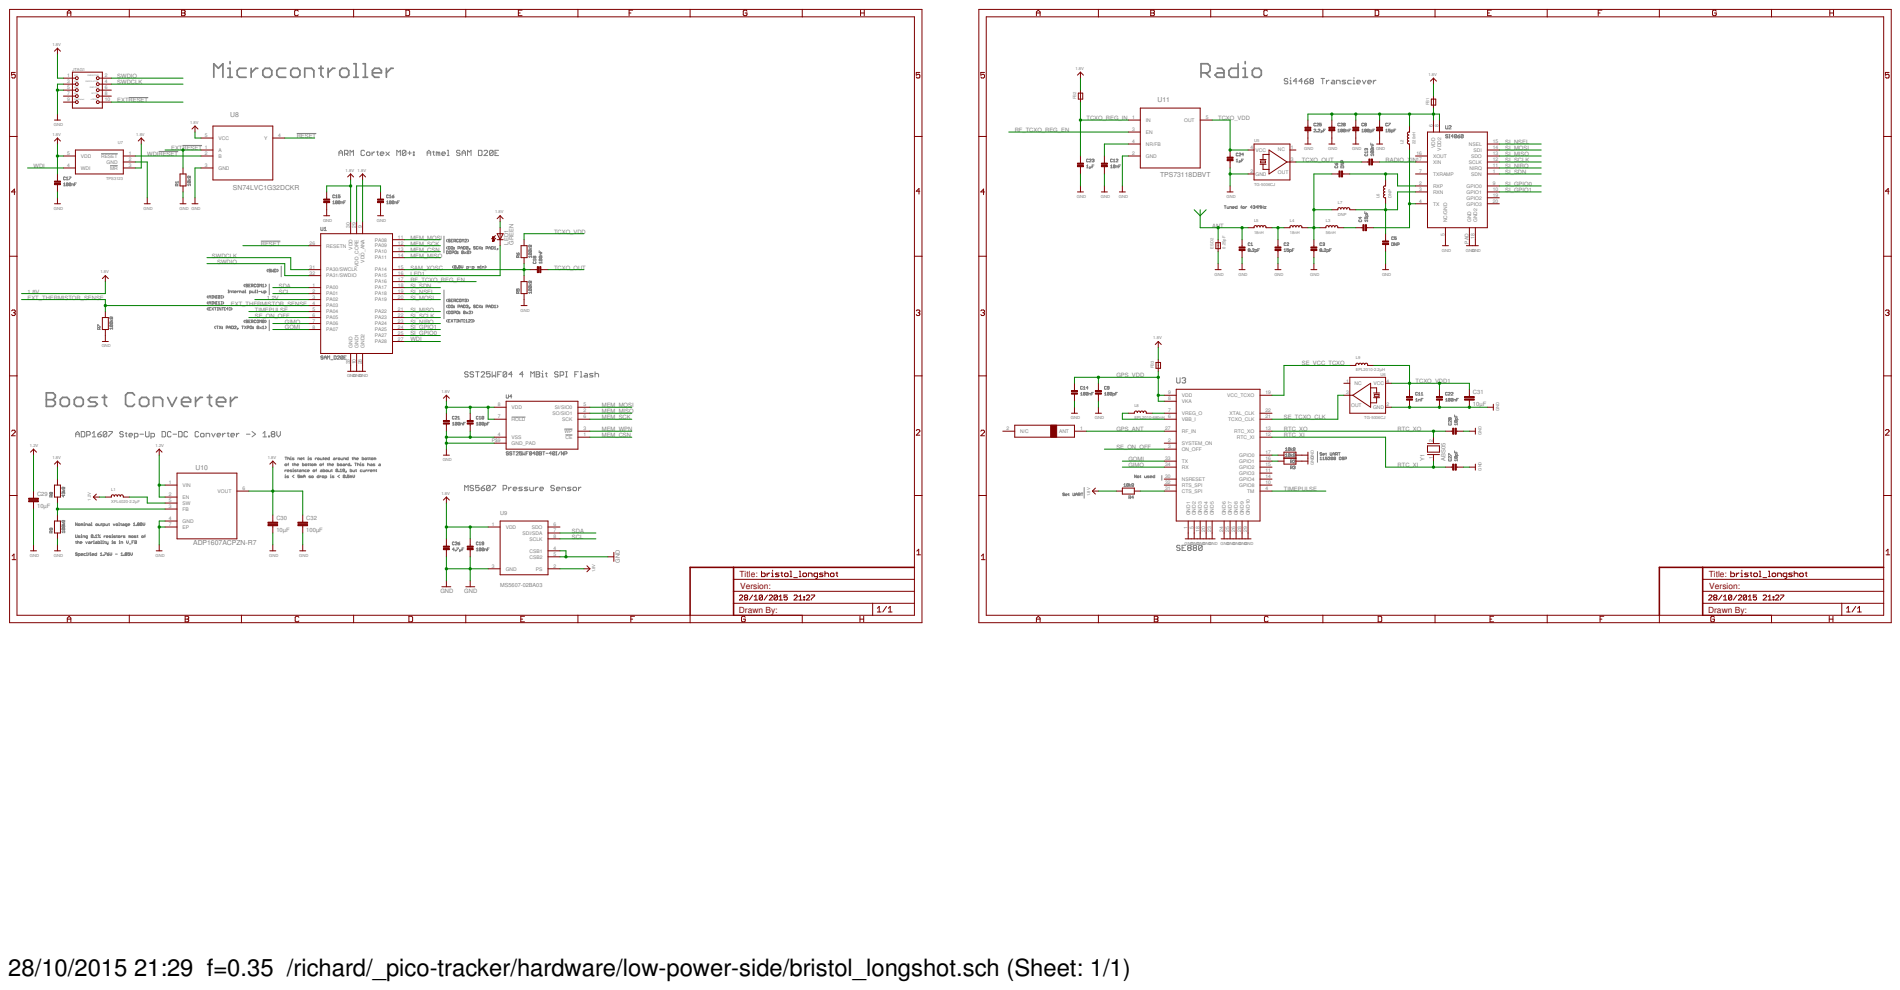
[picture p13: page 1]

nRESET NC/TDI SWO/TDO

28/10/2015 21:29 f=0.35 /richard/_pico-tracker/hardware/low-power-side/bristol_longshot.sch (Sheet: 1/1)

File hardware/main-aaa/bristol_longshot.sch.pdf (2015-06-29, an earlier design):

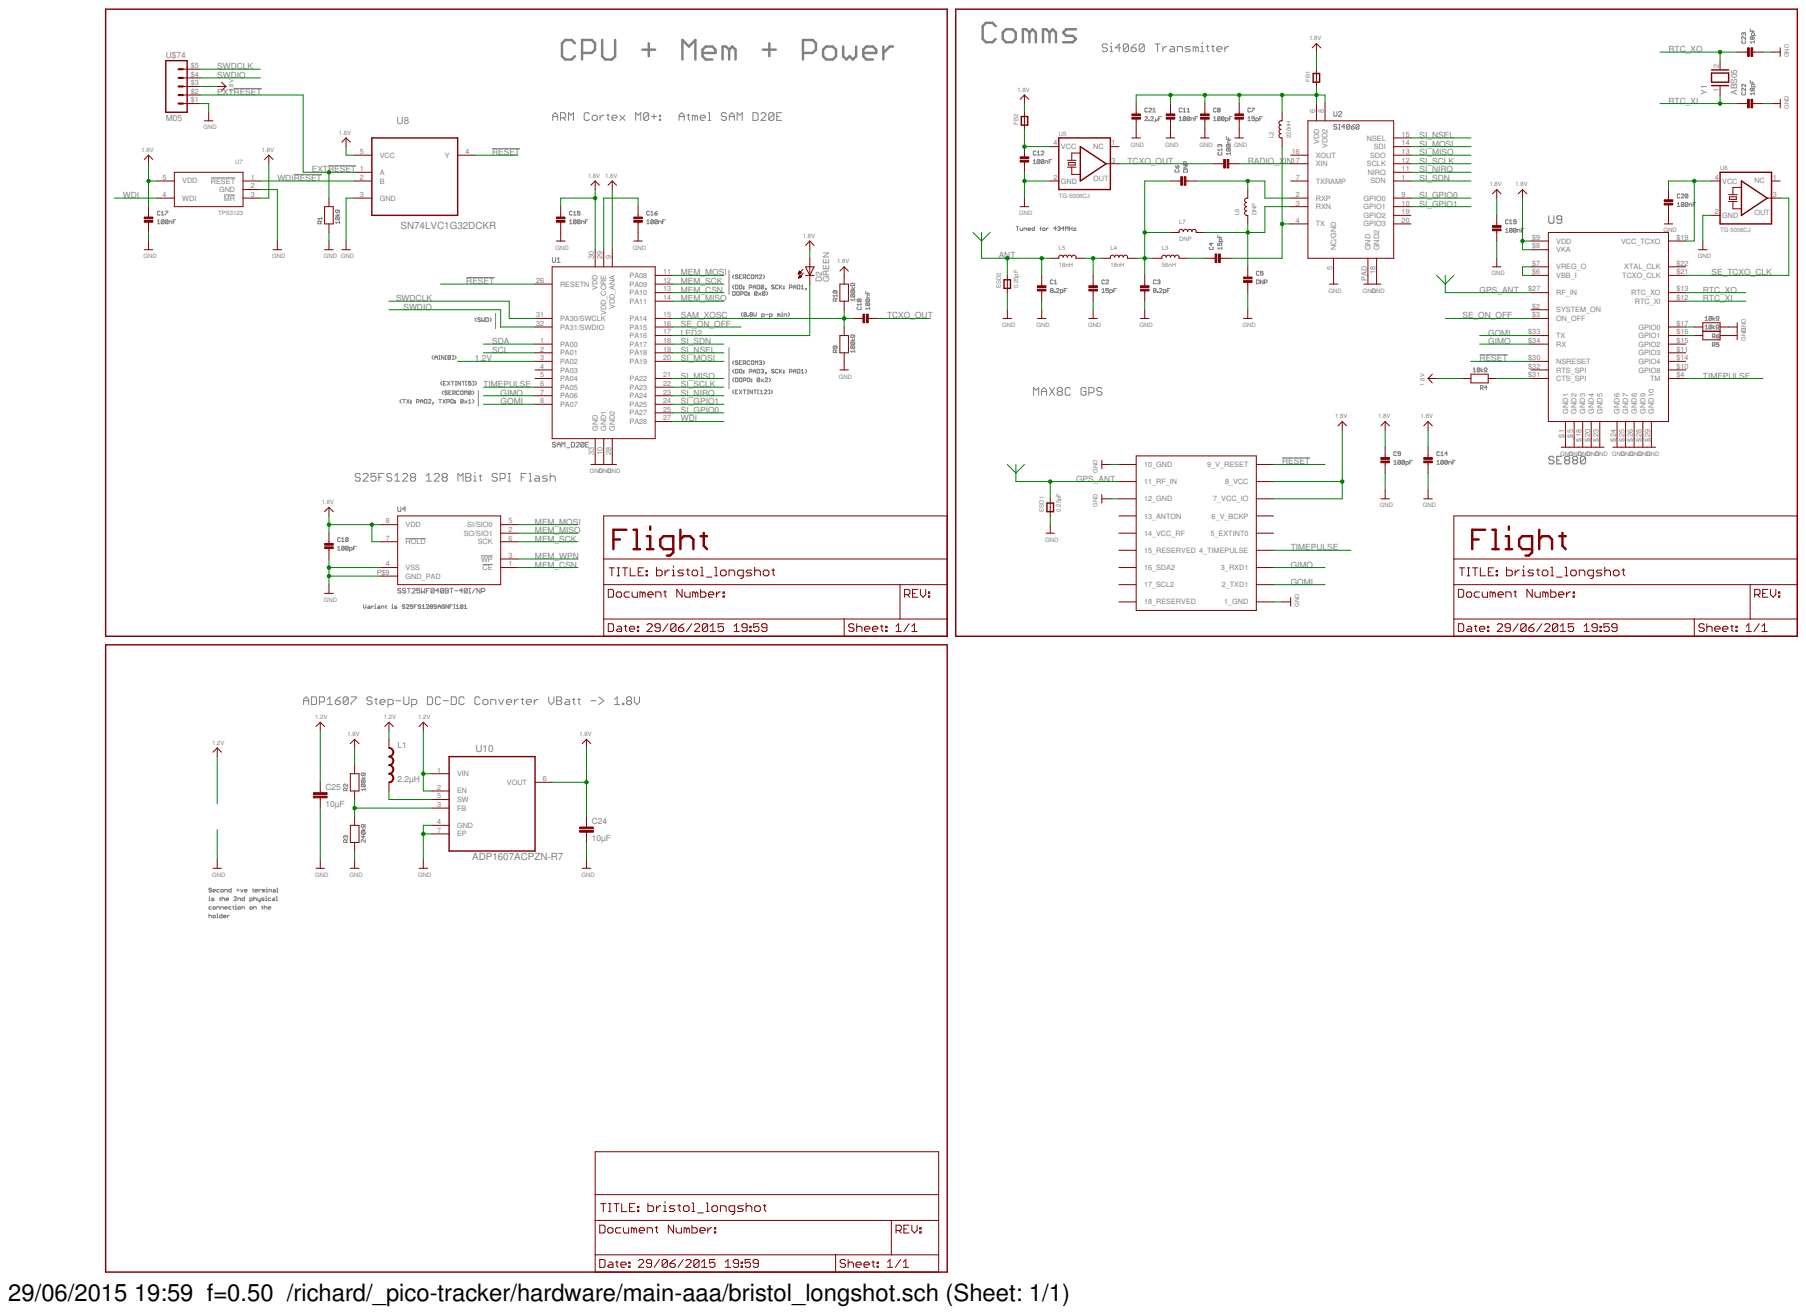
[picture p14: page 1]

TG-5006CJ GND GND GND

29/06/2015 19:59 f=0.50 /richard/_pico-tracker/hardware/main-aaa/bristol_longshot.sch (Sheet: 1/1)

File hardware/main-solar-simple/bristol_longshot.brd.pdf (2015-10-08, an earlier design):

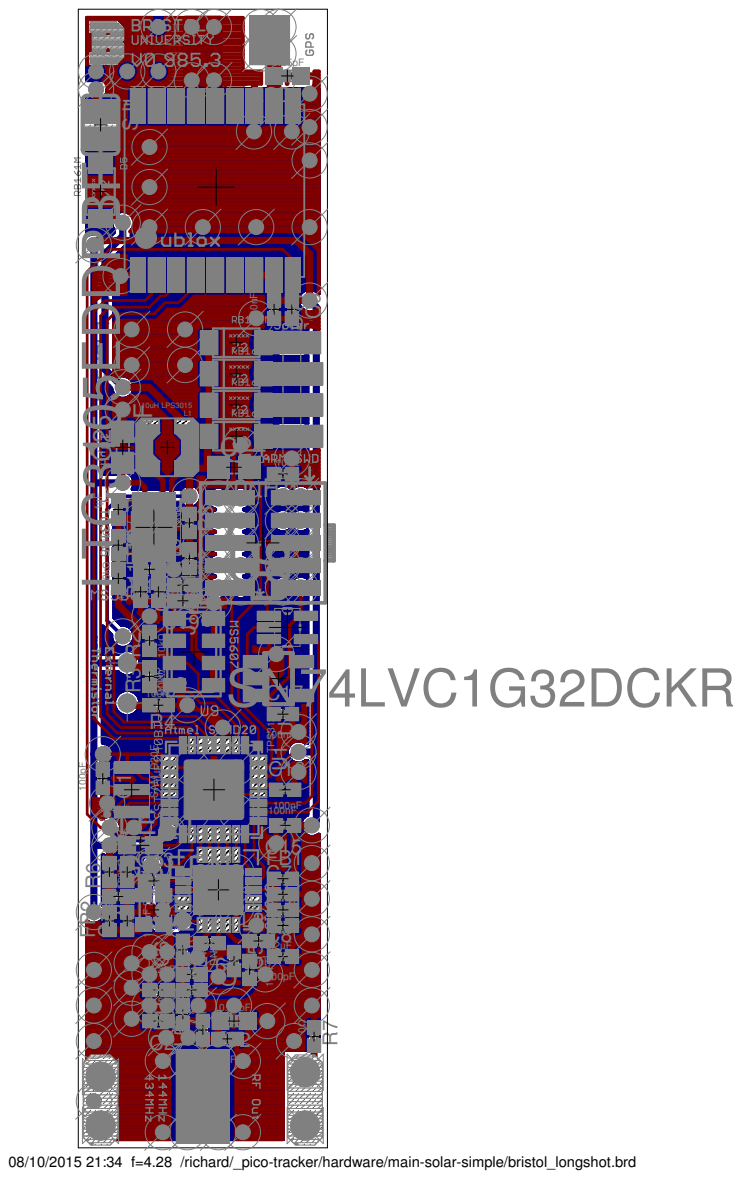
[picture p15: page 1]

1 0nF
100nF

C21
L2
L6 C
L3 4 8.2pF
C3 0.25pF 56nH
C1

DNPDNP DNP DNP

08/10/2015 21:34 f=4.28 /richard/_pico-tracker/hardware/main-solar-simple/bristol_longshot.brd

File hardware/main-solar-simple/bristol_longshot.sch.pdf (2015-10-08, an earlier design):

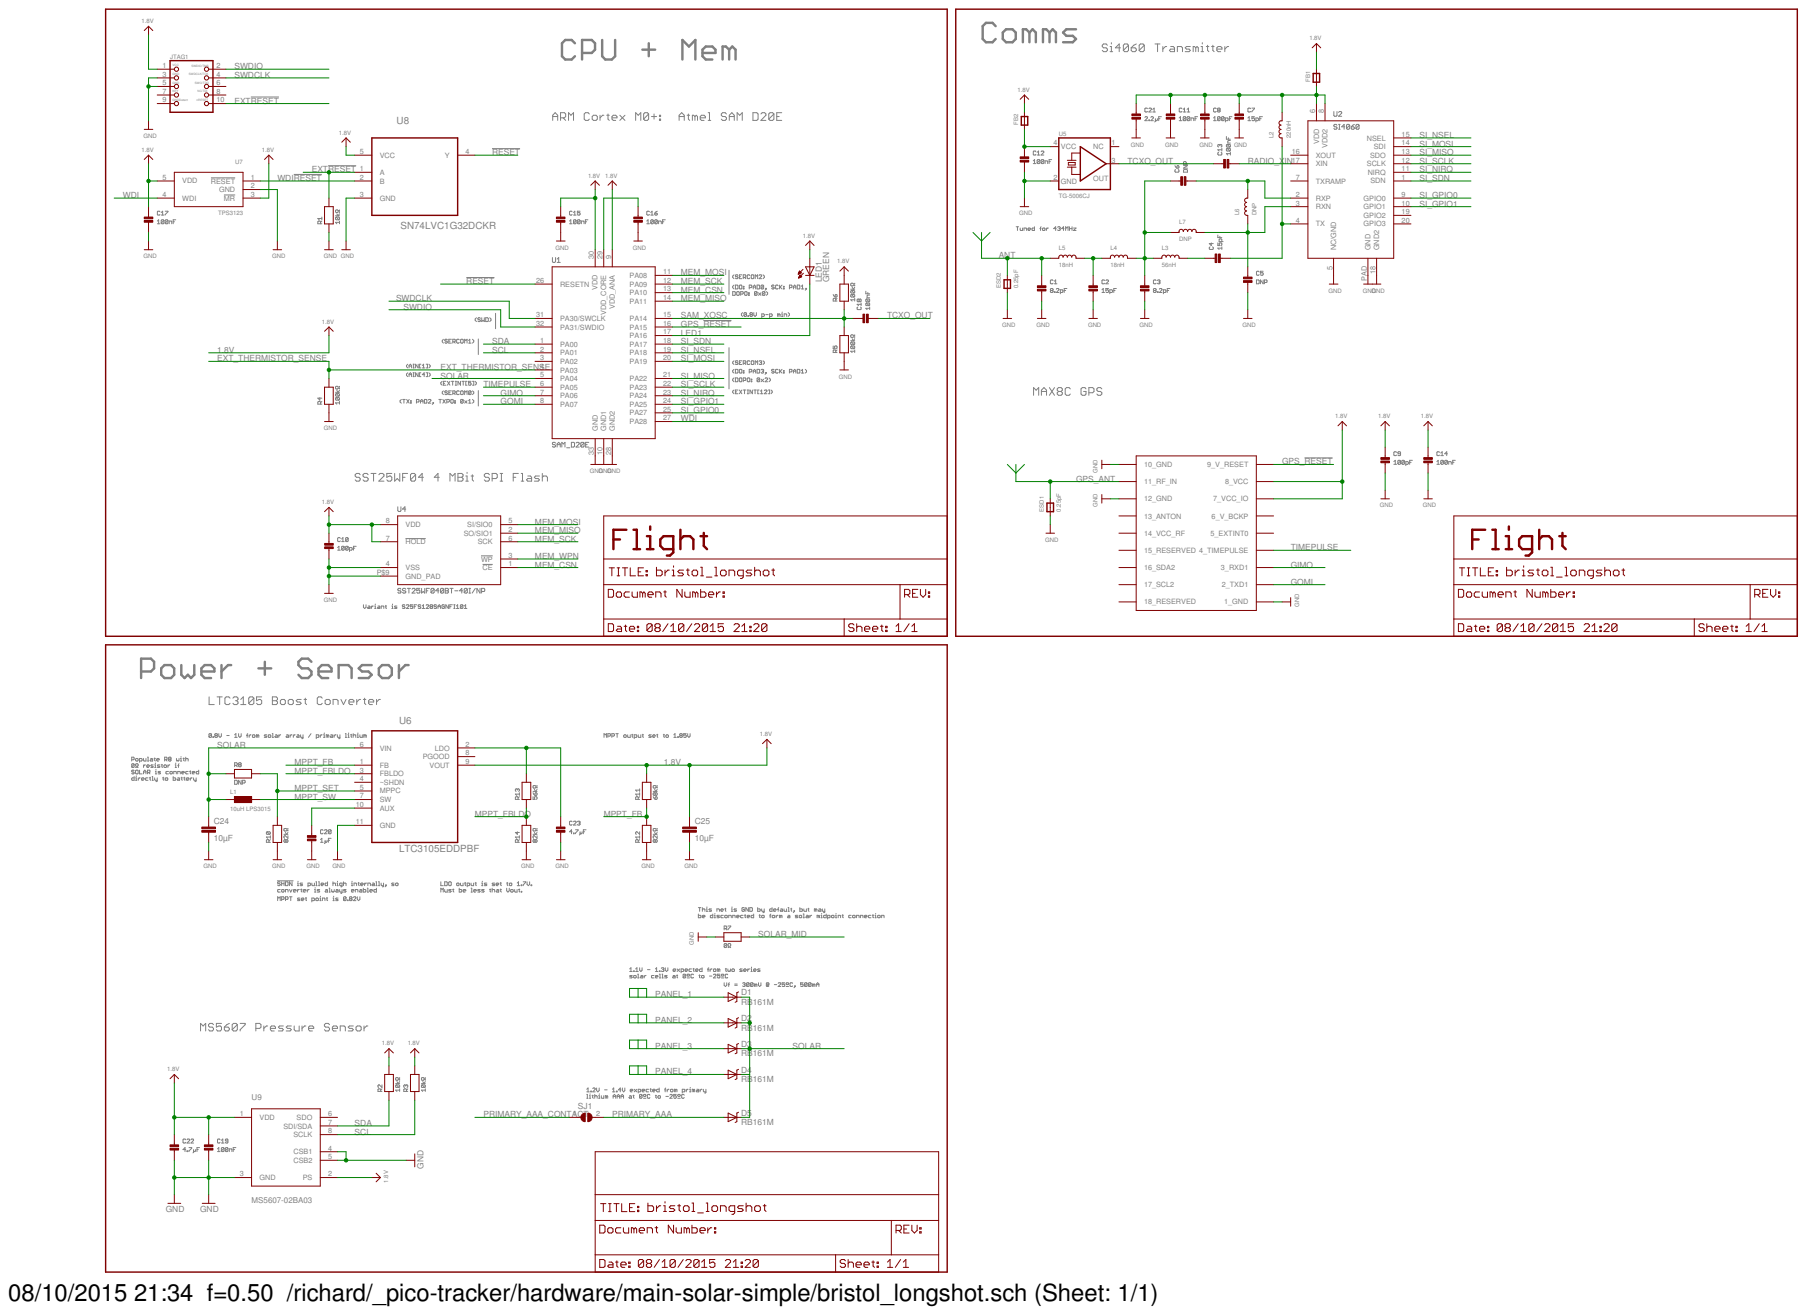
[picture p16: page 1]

nRESET NC/TDI SWO/TDO

08/10/2015 21:34 f=0.50 /richard/_pico-tracker/hardware/main-solar-simple/bristol_longshot.sch (Sheet: 1/1)

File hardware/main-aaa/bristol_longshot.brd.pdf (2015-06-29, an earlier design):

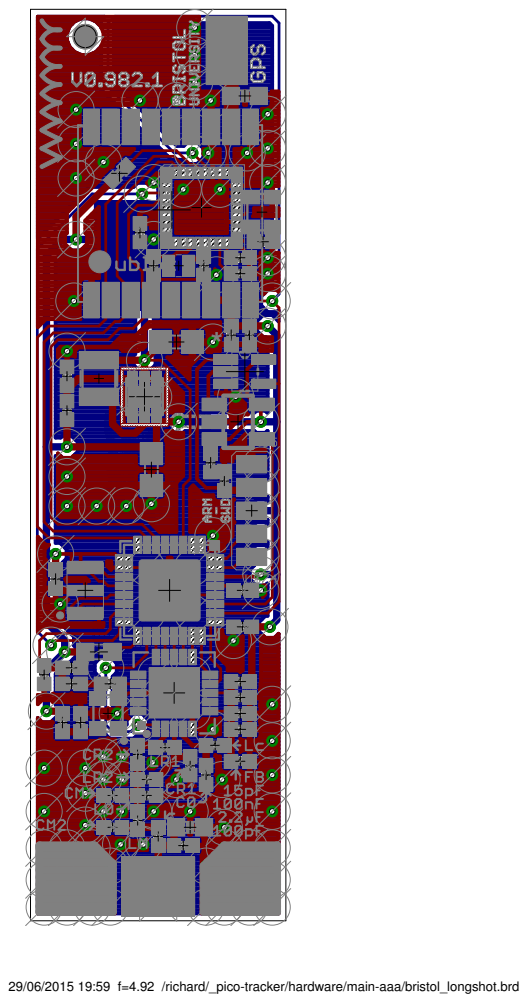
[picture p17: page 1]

29/06/2015 19:59 f=4.92 /richard/_pico-tracker/hardware/main-aaa/bristol_longshot.brd

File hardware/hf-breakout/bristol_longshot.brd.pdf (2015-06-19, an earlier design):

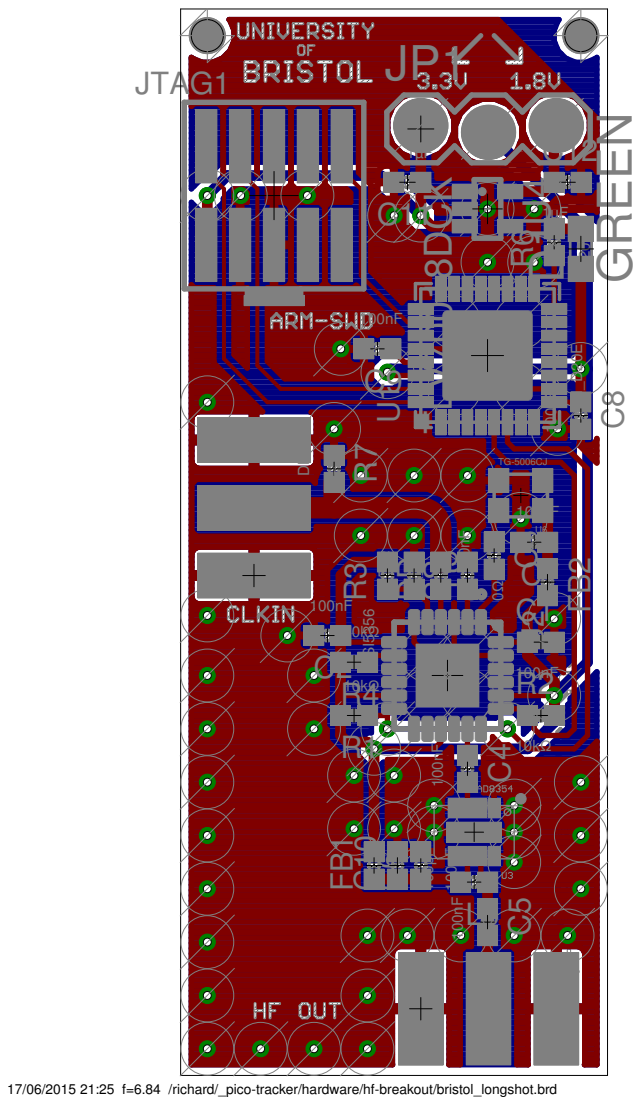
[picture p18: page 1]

C2 | R2
10kΩ

17/06/2015 21:25 f=6.84 /richard/_pico-tracker/hardware/hf-breakout/bristol_longshot.brd

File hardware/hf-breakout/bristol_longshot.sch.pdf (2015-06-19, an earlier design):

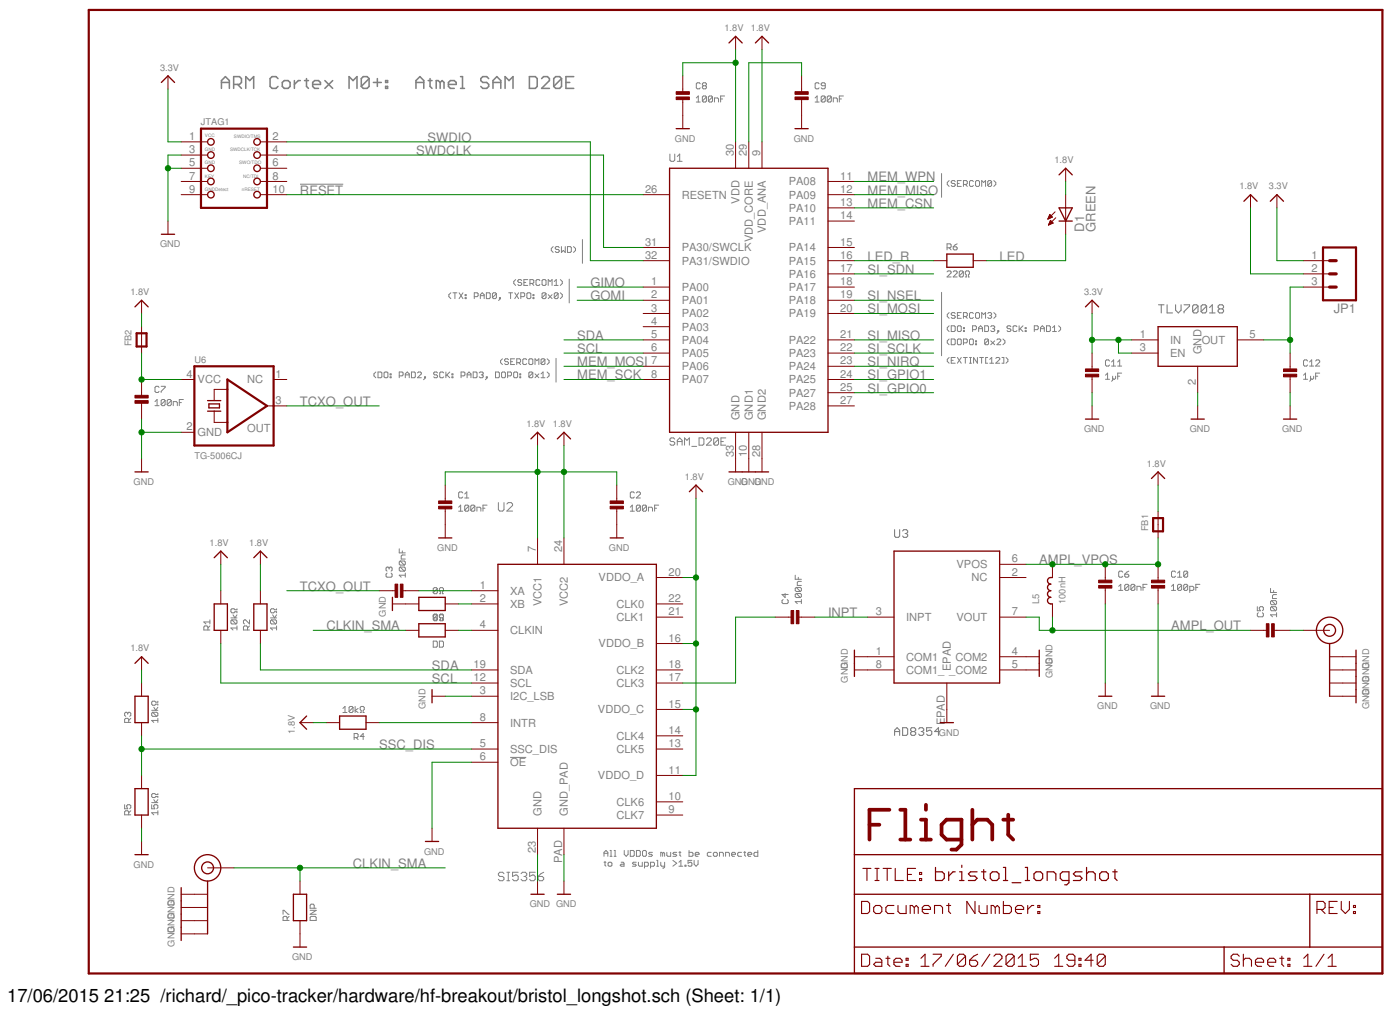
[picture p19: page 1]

nRESET NC/TDI SWO/TDO

17/06/2015 21:25 /richard/_pico-tracker/hardware/hf-breakout/bristol_longshot.sch (Sheet: 1/1)

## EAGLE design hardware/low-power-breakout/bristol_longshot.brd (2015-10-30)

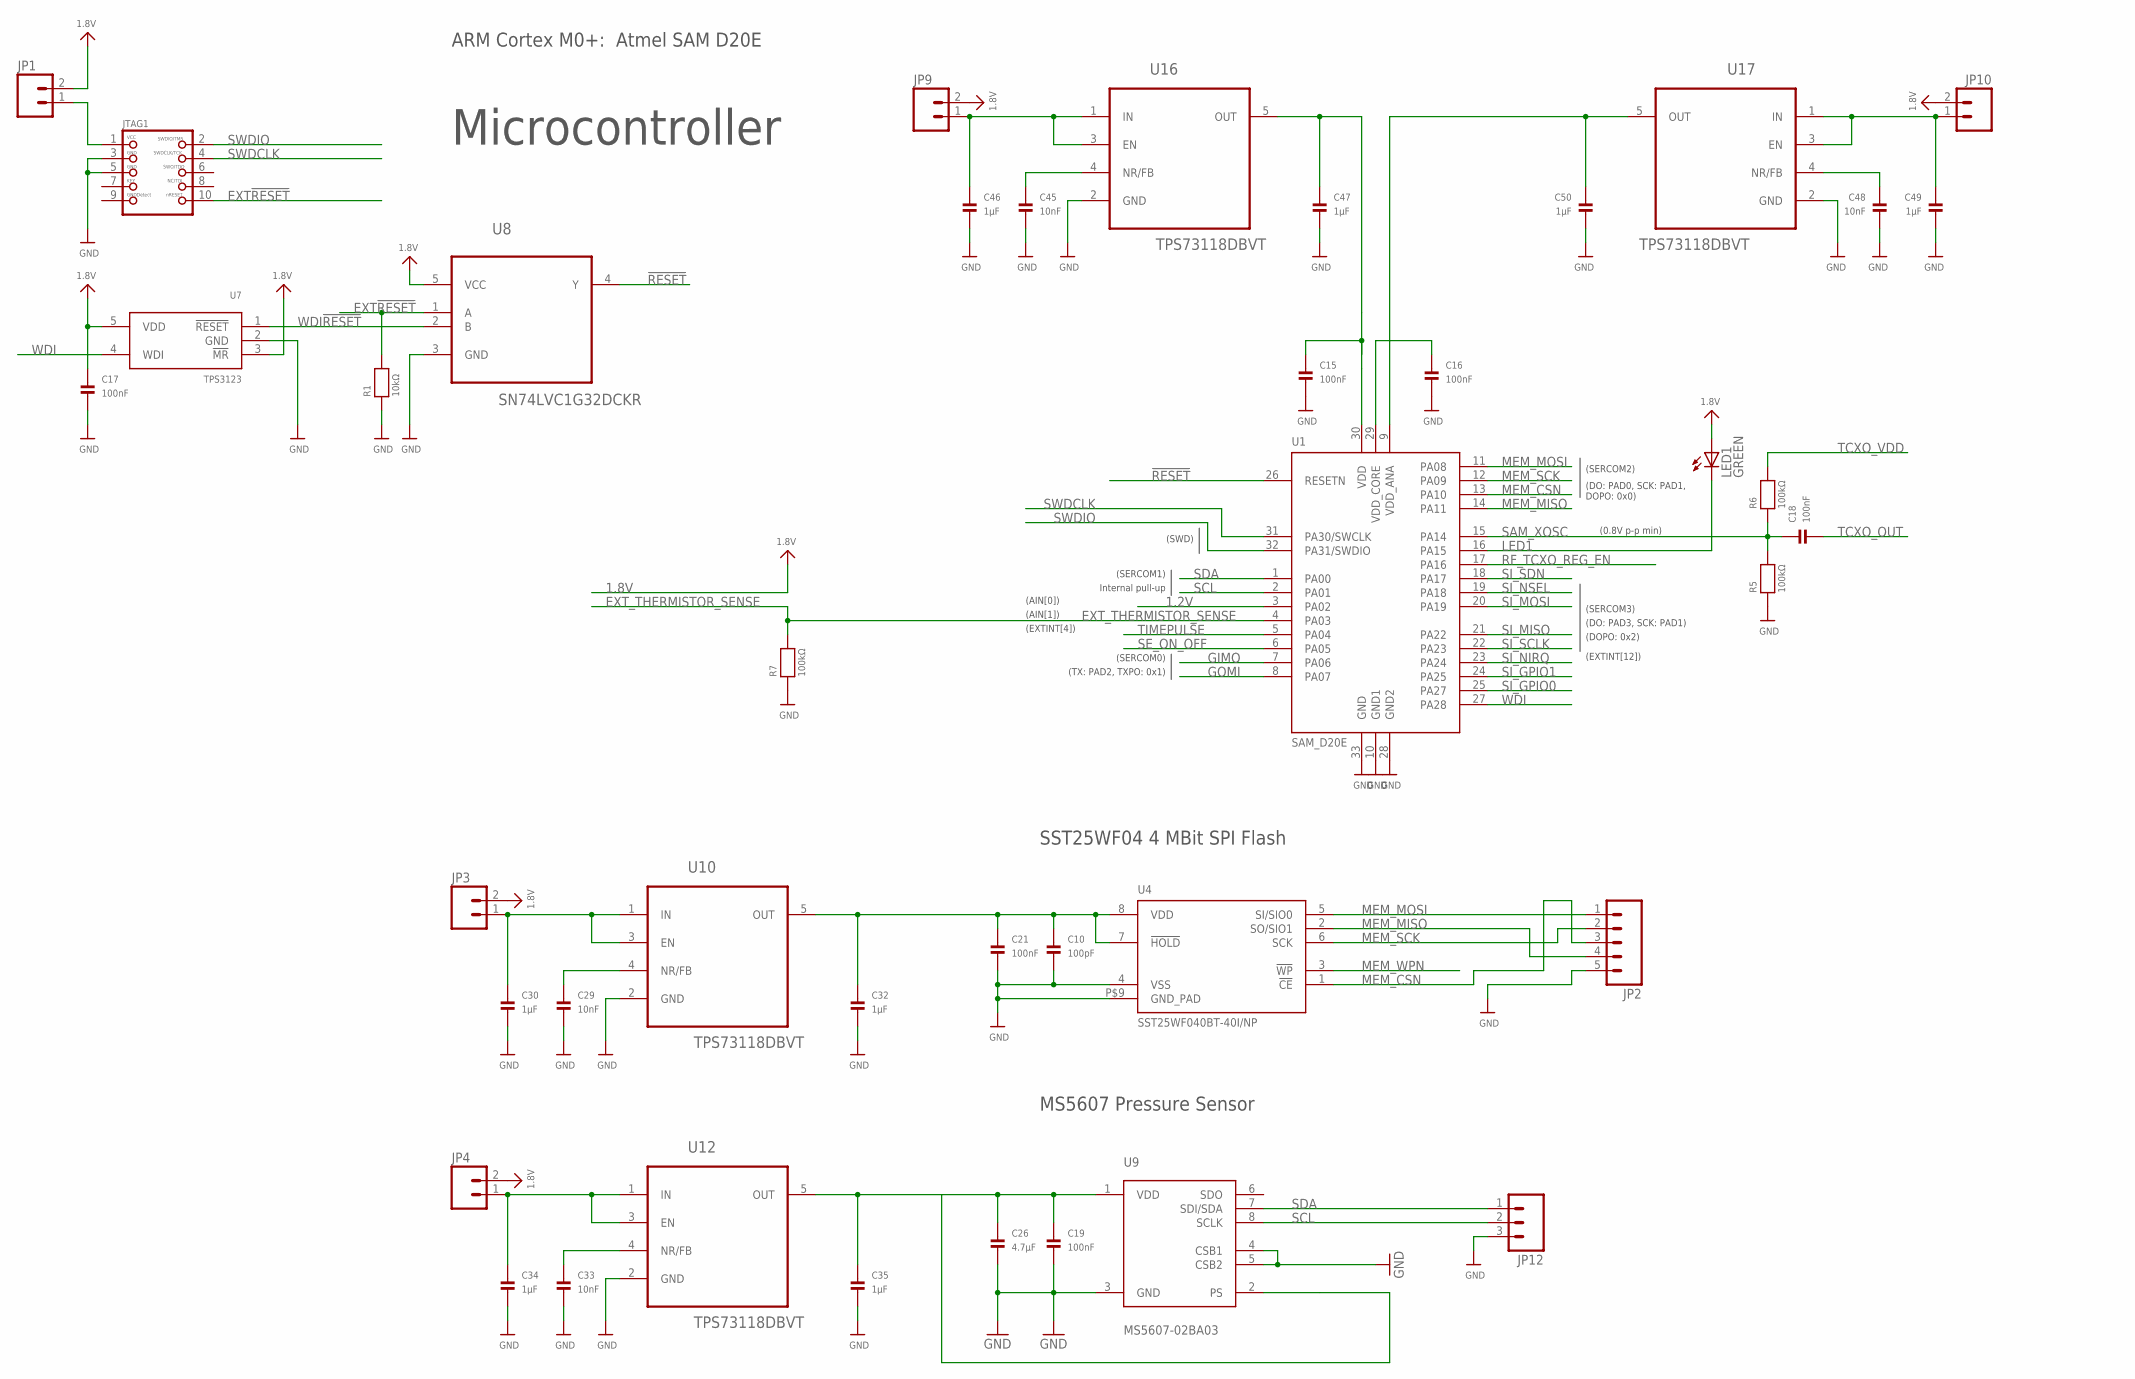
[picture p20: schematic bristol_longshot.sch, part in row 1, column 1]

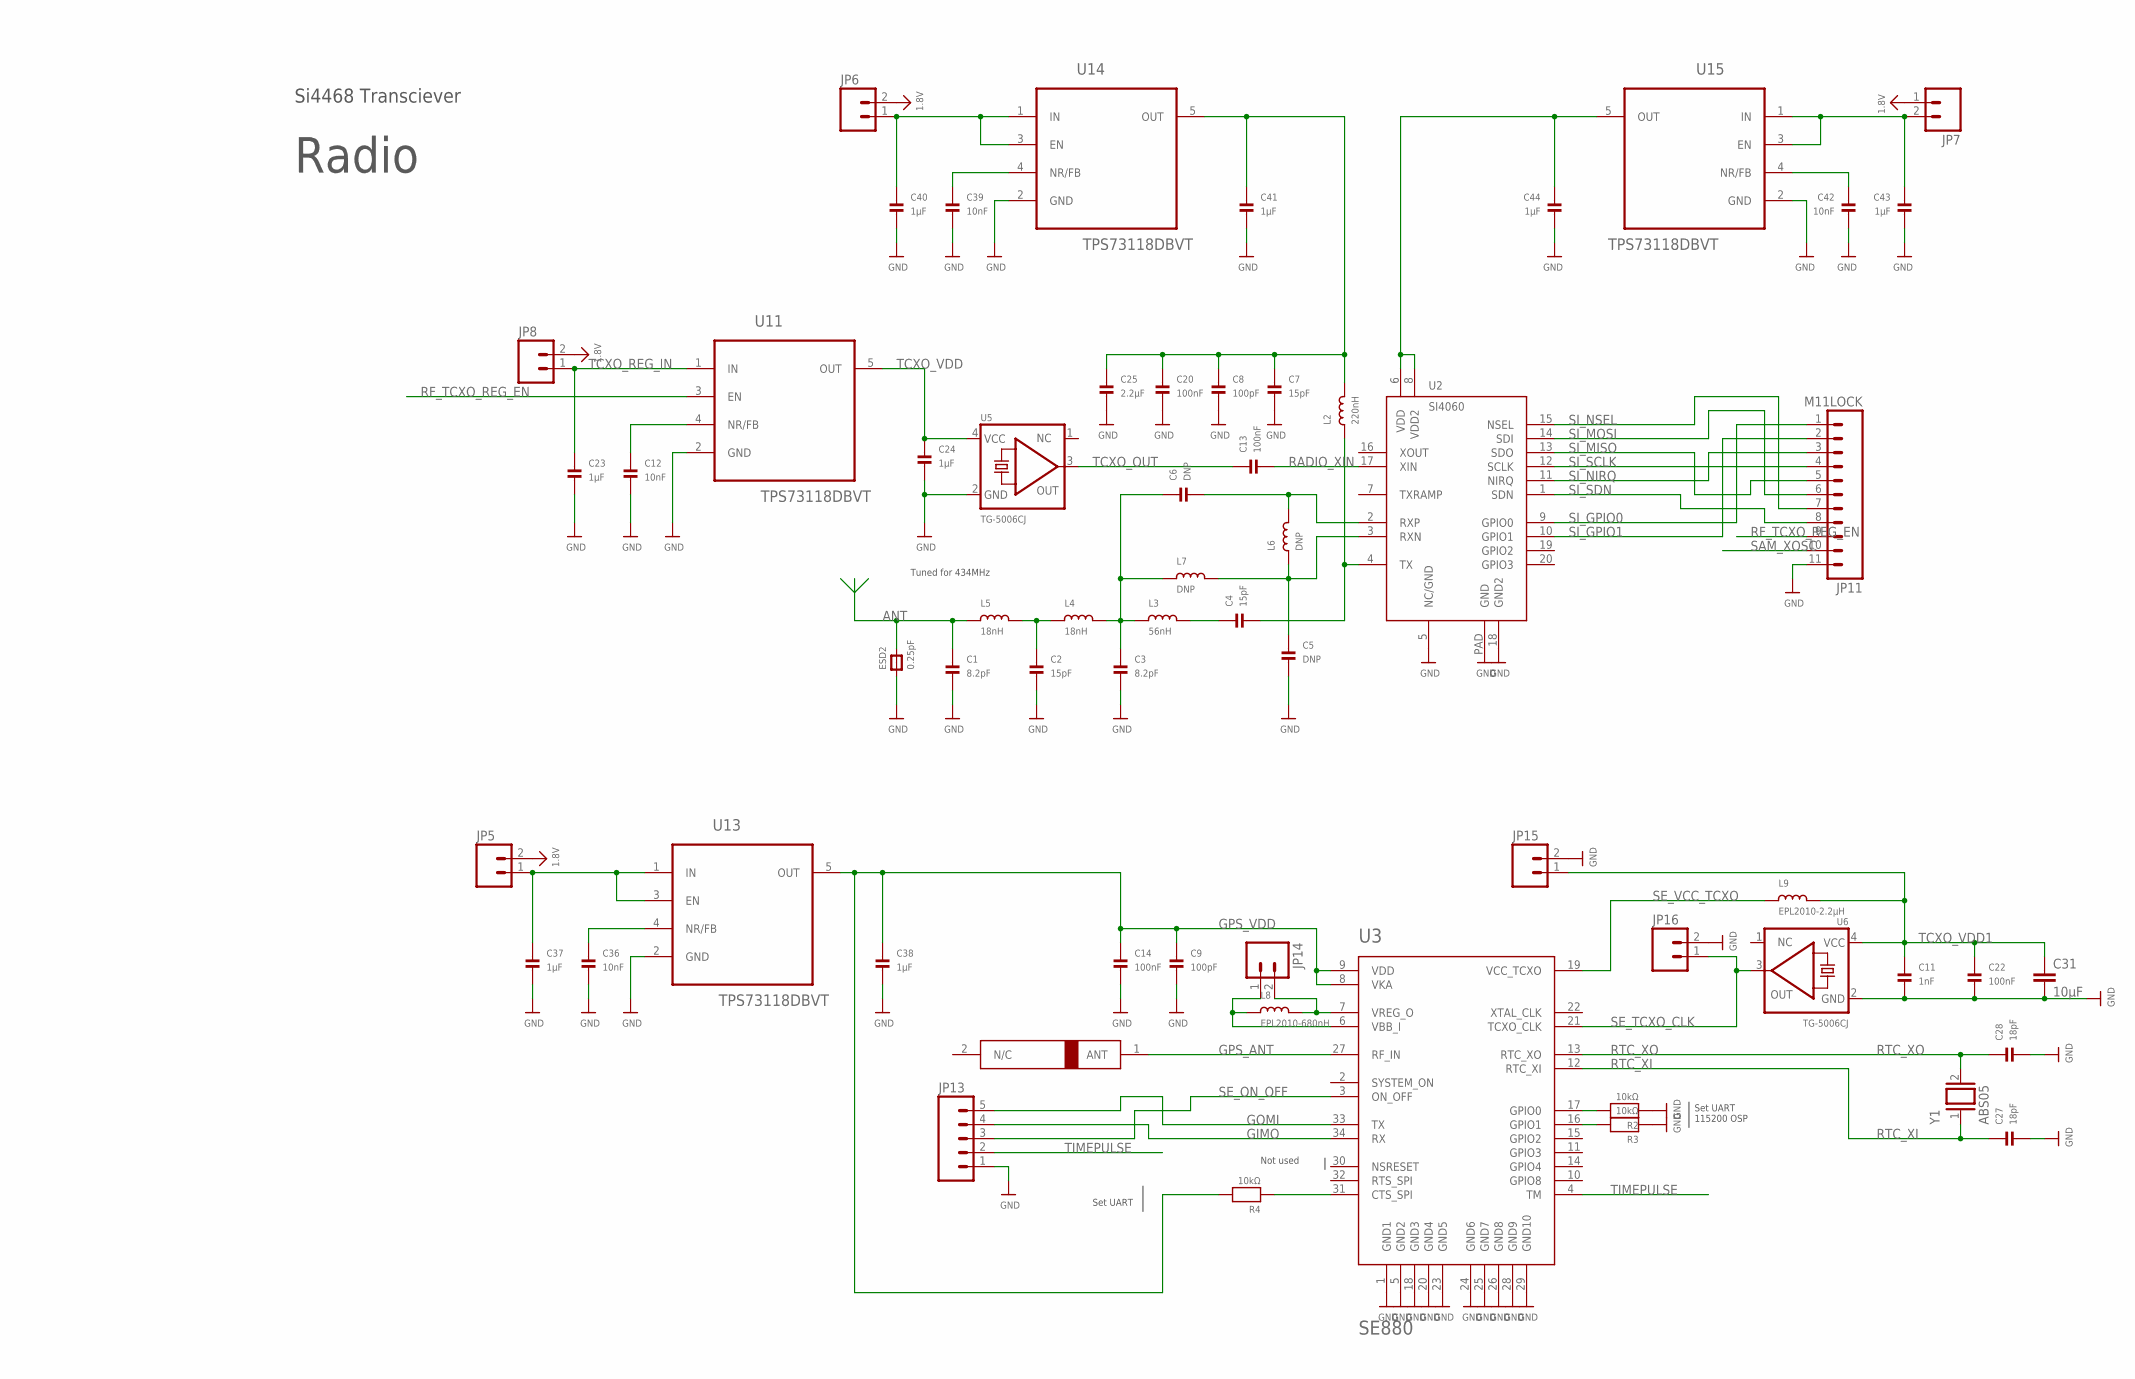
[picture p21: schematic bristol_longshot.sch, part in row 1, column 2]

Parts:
A1: 1575AT43A40
C1, C3: 8.2pF; _0402@2
C2, C4, C7: 15pF; _0402@2
C5, C6: DNP; _0402@2
C8, C9, C10: 100pF; _0402@2
C11: 1nF; _0402@2
C12, C29, C33, C36, C39, C42, C45, C48: 10nF; _0402@2
C13, C14, C15, C16, C17, C18, C19, C20, C21, C22: 100nF; _0402@2
C23, C24, C30, C32, C34, C35, C37, C38, C40, C41, C43, C44, C46, C47, C49, C50: 1µF; _0402@2
C25: 2.2µF; _0402@2
C26: 4.7µF; _0402@2
C27, C28: 18pF; _0402@2
C31: 10µF; C0603K
ESD2: 0.25pF; _0603MP
JP1, JP3, JP4, JP5, JP6, JP7, JP8, JP9, JP10, JP14, JP15, JP16: M02LOCK; 1X02_LOCK
JP2, JP13: M05LOCK; 1X05_LOCK
JP11: M11LOCK; 1X11_LOCK
JP12: M03LOCK; 1X03_LOCK
JTAG1: JTAG-CORTEXM3SMT; 2X05_1.27MM_SMT
L2: 220nH; _0402@1
L3: 56nH; _0402@1
L4, L5: 18nH; _0402@1
L6, L7: DNP; _0402@1
L8: EPL2010-680nH; EPL2010
L9: EPL2010-2.2µH; EPL2010
LED1: GREEN; CHIPLED_0603
R1, R2, R3, R4: 10kΩ; _0402
R5, R6, R7: 100kΩ; _0402
U1: SAM_D20E; QFN32_5MM
U2: SI4060; QFN20
U3: SE880
U4: SST25WF040BT-40I/NP; USON-8
U5, U6: TG-5006CJ; TC-5006CJ
U7: TPS3123; SOT23-5
U8: SN74LVC1G32DCKR; SOT65P210X110-5N
U9: MS5607-02BA03
U10, U11, U12, U13, U14, U15, U16, U17: TPS73118DBVT; SOT95P280X145-5N
Y1: ABS05

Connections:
1.2V: U1.3 (PA02)
1.8V: C17.1, JP1.2, JP3.2, JP4.2, JP5.2, JP6.2, JP7.1, JP8.2, JP9.2, JP10.2, LED1.A, U7.3 (!MR), U7.5 (VDD), U8.5 (VCC)
!RESET: U1.26 (RESETN), U8.4 (Y)
ANT: C1.1, ESD2.2, L5.1
EXT!RESET: JTAG1.10, R1.2, U8.1 (A)
EXT_THERMISTOR_SENSE: R7.2, U1.4 (PA03)
FILTER1: C3.1, C6.1, L3.1, L4.2, L7.1
FILTER2: C2.1, L4.1, L5.2
GIMO: JP13.4, U1.7 (PA06), U3.34 (RX)
GND: C1.2, C2.2, C3.2, C5.2, C7.2, C8.2, C9.2, C10.2, C11.2, C12.2, C14.2, C15.2, C16.2, C17.2, C19.2, C20.2, C21.2, C22.2, C23.2, C24.2, C25.2, C26.2, C27.2, C28.2, C29.2, C30.2, C31.2, C32.2, C33.2, C34.2, C35.2, C36.2, C37.2, C38.2, C39.2, C40.2, C41.2, C42.2, C43.2, C44.2, C45.2, C46.2, C47.2, C48.2, C49.2, C50.2, ESD2.1, JP2.5, JP11.11, JP12.3, JP13.1, JP15.2, JP16.2, JTAG1.3, JTAG1.5, R1.1, R2.1, R3.1, R5.1, R7.1, U1.10 (GND1), U1.28 (GND2), U1.33 (GND), U2.5 (NC/GND), U2.18 (GND2), U2.PAD (GND), U3.1 (GND1), U3.5 (GND2), U3.18 (GND3), U3.20 (GND4), U3.23 (GND5), U3.24 (GND6), U3.25 (GND7), U3.26 (GND8), U3.28 (GND9), U3.29 (GND10), U4.4 (VSS), U4.P$9 (GND_PAD), U5.2 (GND), U6.2 (GND), U7.2 (GND), U8.3 (GND), U9.3 (GND), U9.4 (CSB1), U9.5 (CSB2), U10.2 (GND), U11.2 (GND), U12.2 (GND), U13.2 (GND), U14.2 (GND), U15.2 (GND), U16.2 (GND), U17.2 (GND)
GOMI: JP13.5, U1.8 (PA07), U3.33 (TX)
GPS_ANT: A1.1 (ANT), U3.27 (RF_IN)
GPS_VDD: C9.1, C14.1, C38.1, R4.2, U3.8 (VKA), U3.9 (VDD), U13.5 (OUT)
LED1: LED1.C, U1.16 (PA15)
MEM_CSN: JP2.3, U1.13 (PA10), U4.1 (!CE)
MEM_MISO: JP2.4, U1.14 (PA11), U4.2 (SO/SIO1)
MEM_MOSI: JP2.1, U1.11 (PA08), U4.5 (SI/SIO0)
MEM_SCK: JP2.2, U1.12 (PA09), U4.6 (SCK)
MEM_WPN: U4.3 (!WP)
unnamed: JP1.1, JTAG1.1
unnamed: C30.1, JP3.1, U10.1 (IN), U10.3 (EN)
unnamed: C29.1, U10.4 (NR/FB)
unnamed: C10.1, C21.1, C32.1, U4.7 (!HOLD), U4.8 (VDD), U10.5 (OUT)
unnamed: C34.1, JP4.1, U12.1 (IN), U12.3 (EN)
unnamed: C33.1, U12.4 (NR/FB)
unnamed: C19.1, C26.1, C35.1, U9.1 (VDD), U9.2 (PS), U12.5 (OUT)
unnamed: C37.1, JP5.1, U13.1 (IN), U13.3 (EN)
unnamed: C36.1, U13.4 (NR/FB)
unnamed: C46.1, JP9.1, U16.1 (IN), U16.3 (EN)
unnamed: C40.1, JP6.1, U14.1 (IN), U14.3 (EN)
unnamed: C39.1, U14.4 (NR/FB)
unnamed: C45.1, U16.4 (NR/FB)
unnamed: C43.1, JP7.2, U15.1 (IN), U15.3 (EN)
unnamed: C42.1, U15.4 (NR/FB)
unnamed: C44.1, U2.6 (VDD), U2.8 (VDD2), U15.5 (OUT)
unnamed: C15.1, C47.1, U1.30 (VDD), U16.5 (OUT)
unnamed: C49.1, JP10.1, U17.1 (IN), U17.3 (EN)
unnamed: C48.1, U17.4 (NR/FB)
unnamed: C50.1, U1.9 (VDD_ANA), U17.5 (OUT)
RADIO_VDD: C7.1, C8.1, C20.1, C25.1, C41.1, L2.2, U14.5 (OUT)
RADIO_XIN: C13.2, U2.17 (XIN)
RF_OUT: C4.2, L2.1, U2.4 (TX)
RF_TANK: C4.1, L3.2
RF_TCXO_REG_EN: JP11.9, U1.17 (PA16), U11.3 (EN)
RTC_XI: C27.1, U3.12 (RTC_XI), Y1.1
RTC_XO: C28.1, U3.13 (RTC_XO), Y1.2
RXN: C5.1, L6.1, L7.2, U2.3 (RXN)
RXP: C6.2, L6.2, U2.2 (RXP)
SAM_XOSC: C18.1, JP11.10, R5.2, R6.1, U1.15 (PA14)
SCL: JP12.2, U1.2 (PA01), U9.8 (SCLK)
SDA: JP12.1, U1.1 (PA00), U9.7 (SDI/SDA)
SE_GPIO0: R2.2, U3.17 (GPIO0)
SE_GPIO1: R3.2, U3.16 (GPIO1)
SE_MODE_PULL: R4.1, U3.31 (CTS_SPI)
SE_ON_OFF: JP13.3, U1.6 (PA05), U3.3 (ON_OFF)
SE_TCXO_CLK: JP16.1, U3.21 (TCXO_CLK), U6.3 (OUT)
SE_VBB: JP14.1, L8.1, U3.6 (VBB_I)
SE_VCC_TCXO: L9.1, U3.19 (VCC_TCXO)
SE_VREG: JP14.2, L8.2, U3.7 (VREG_O)
SI_GPIO0: JP11.1, U1.25 (PA27), U2.9 (GPIO0)
SI_GPIO1: JP11.2, U1.24 (PA25), U2.10 (GPIO1)
SI_MISO: JP11.5, U1.21 (PA22), U2.13 (SDO)
SI_MOSI: JP11.6, U1.20 (PA19), U2.14 (SDI)
SI_NIRQ: JP11.3, U1.23 (PA24), U2.11 (NIRQ)
SI_NSEL: JP11.7, U1.19 (PA18), U2.15 (NSEL)
SI_SCLK: JP11.4, U1.22 (PA23), U2.12 (SCLK)
SI_SDN: JP11.8, U1.18 (PA17), U2.1 (SDN)
SWDCLK: JTAG1.4, U1.31 (PA30/SWCLK)
SWDIO: JTAG1.2, U1.32 (PA31/SWDIO)
TCXO_OUT: C13.1, C18.2, U5.3 (OUT)
TCXO_REG_IN: C23.1, JP8.1, U11.1 (IN)
TCXO_REG_NR: C12.1, U11.4 (NR/FB)
TCXO_VDD: C24.1, R6.2, U5.4 (VCC), U11.5 (OUT)
TCXO_VDD1: C11.1, C22.1, C31.1, JP15.1, L9.2, U6.4 (VCC)
TIMEPULSE: JP13.2, U1.5 (PA04), U3.4 (TM)
VDD_CORE: C16.1, U1.29 (VDD_CORE)
WDI: U1.27 (PA28), U7.4 (WDI)
WDI!RESET: U7.1 (!RESET), U8.2 (B)

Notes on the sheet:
ARM Cortex M0+: Atmel SAM D20E
(SERCOM3)
(SWD)
(EXTINT[12])
(DO: PAD3, SCK: PAD1)
(DOPO: 0x2)
(SERCOM2)
(DO: PAD0, SCK: PAD1, DOPO: 0x0)
(SERCOM0)
(TX: PAD2, TXPO: 0x1)
SST25WF04 4 MBit SPI Flash
Si4468 Transciever
Tuned for 434MHz
Radio
(0.8V p-p min)
(AIN[1])
(EXTINT[4])
(SERCOM1)
MS5607 Pressure Sensor
Microcontroller
Set UART 115200 OSP
Set UART
Internal pull-up
(AIN[0])
Not used

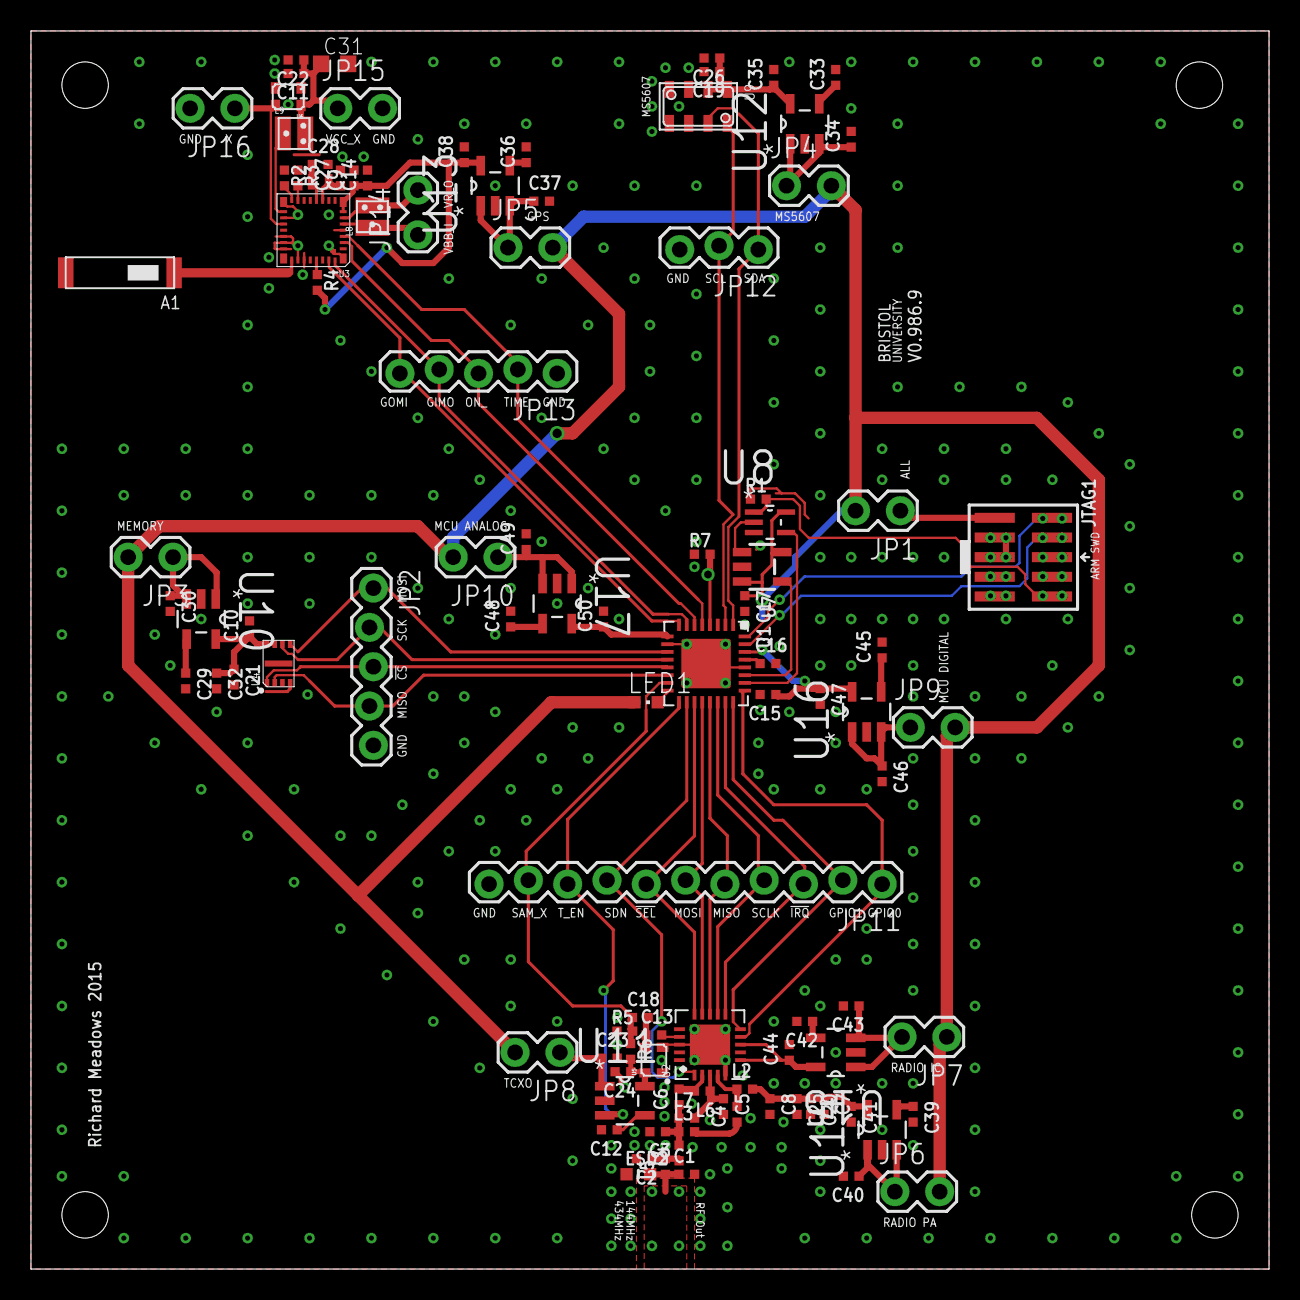
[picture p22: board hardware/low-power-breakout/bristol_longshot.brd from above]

Board: 2 copper layers, 80.0 x 80.0 mm, 103 parts (0 on the bottom side), 76 nets.

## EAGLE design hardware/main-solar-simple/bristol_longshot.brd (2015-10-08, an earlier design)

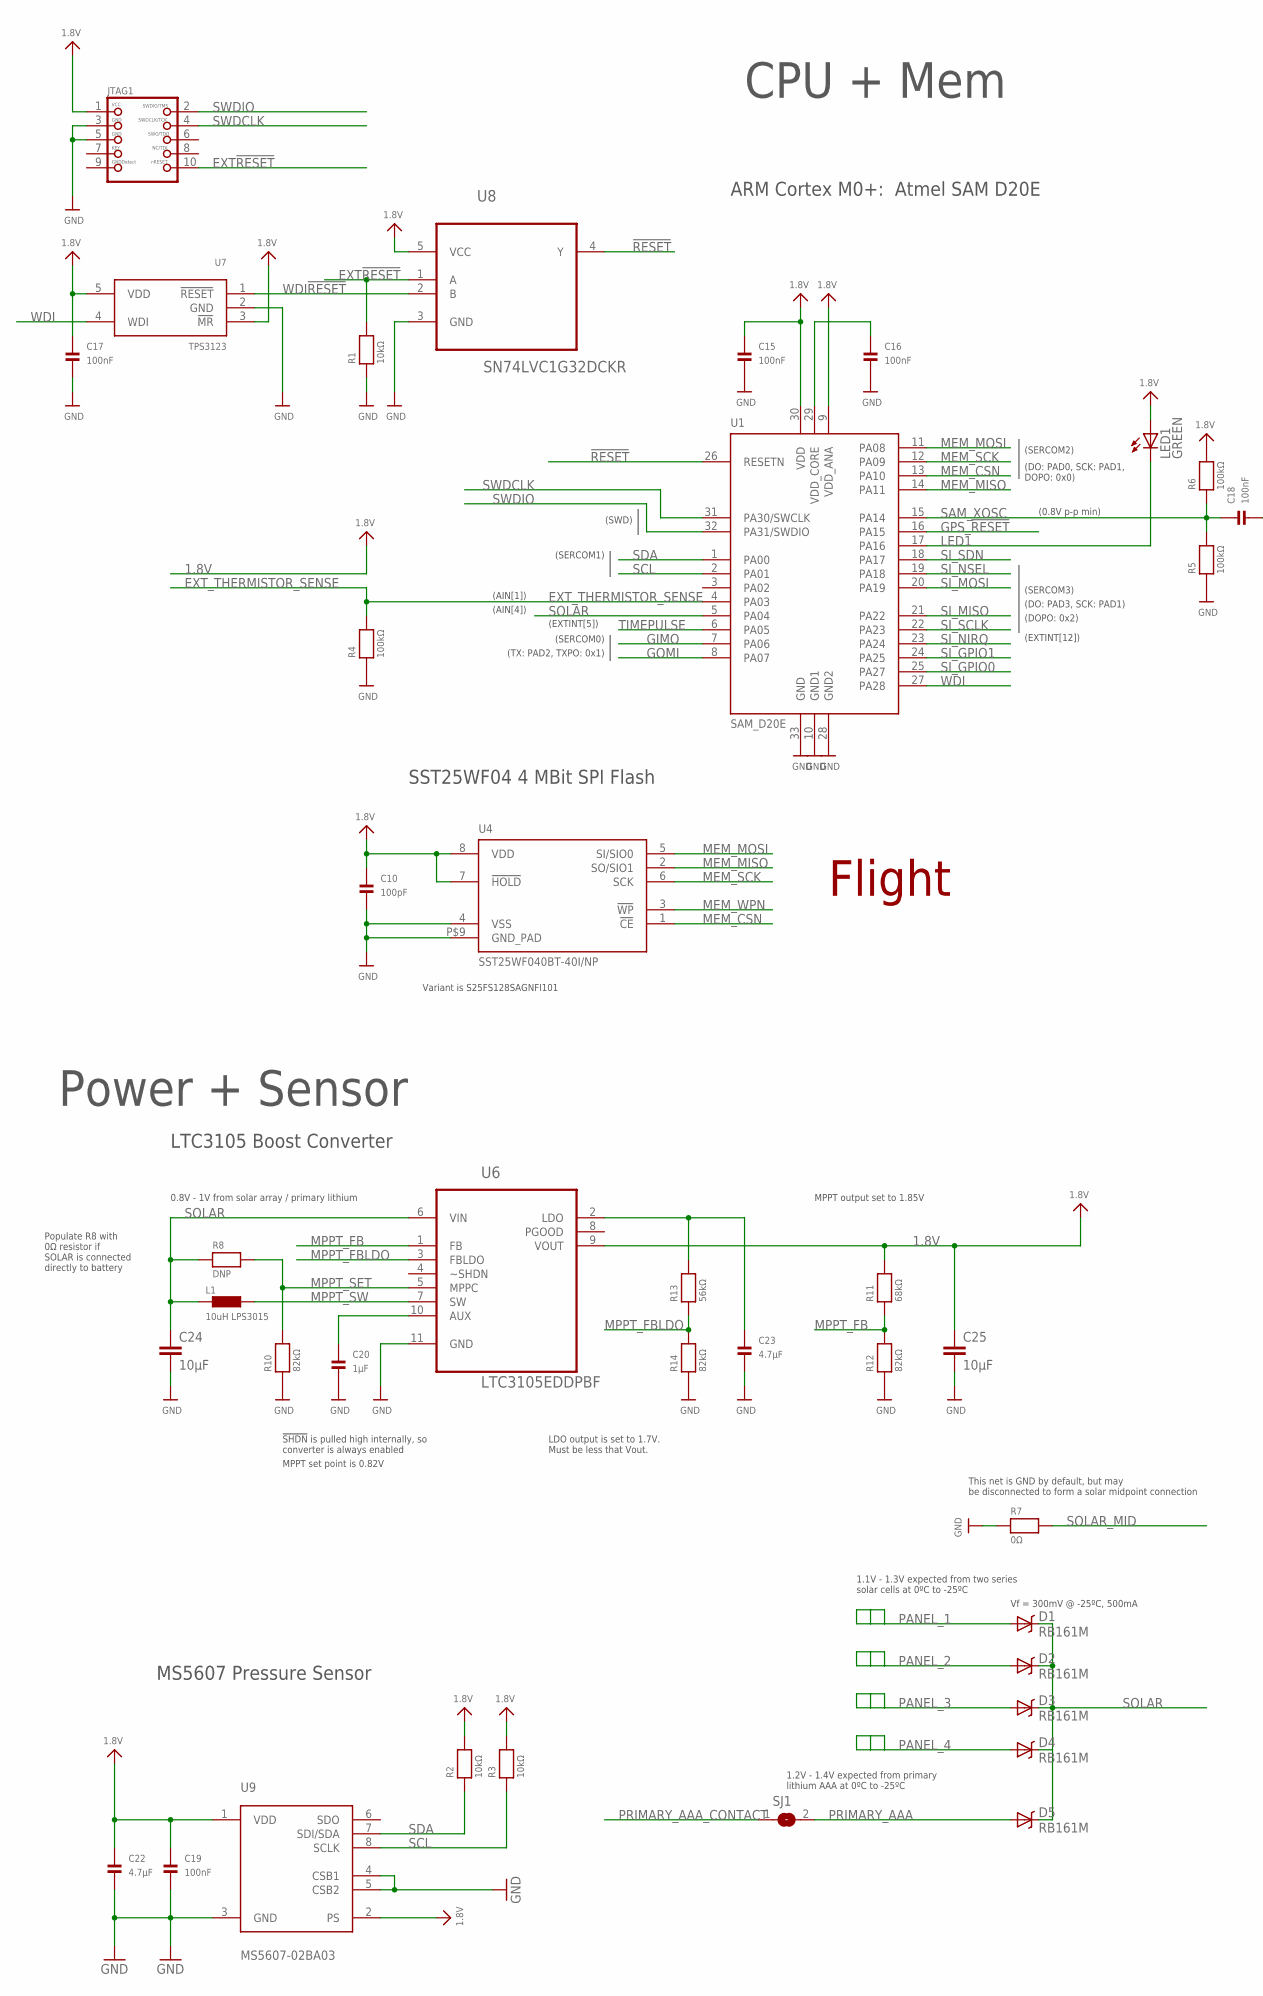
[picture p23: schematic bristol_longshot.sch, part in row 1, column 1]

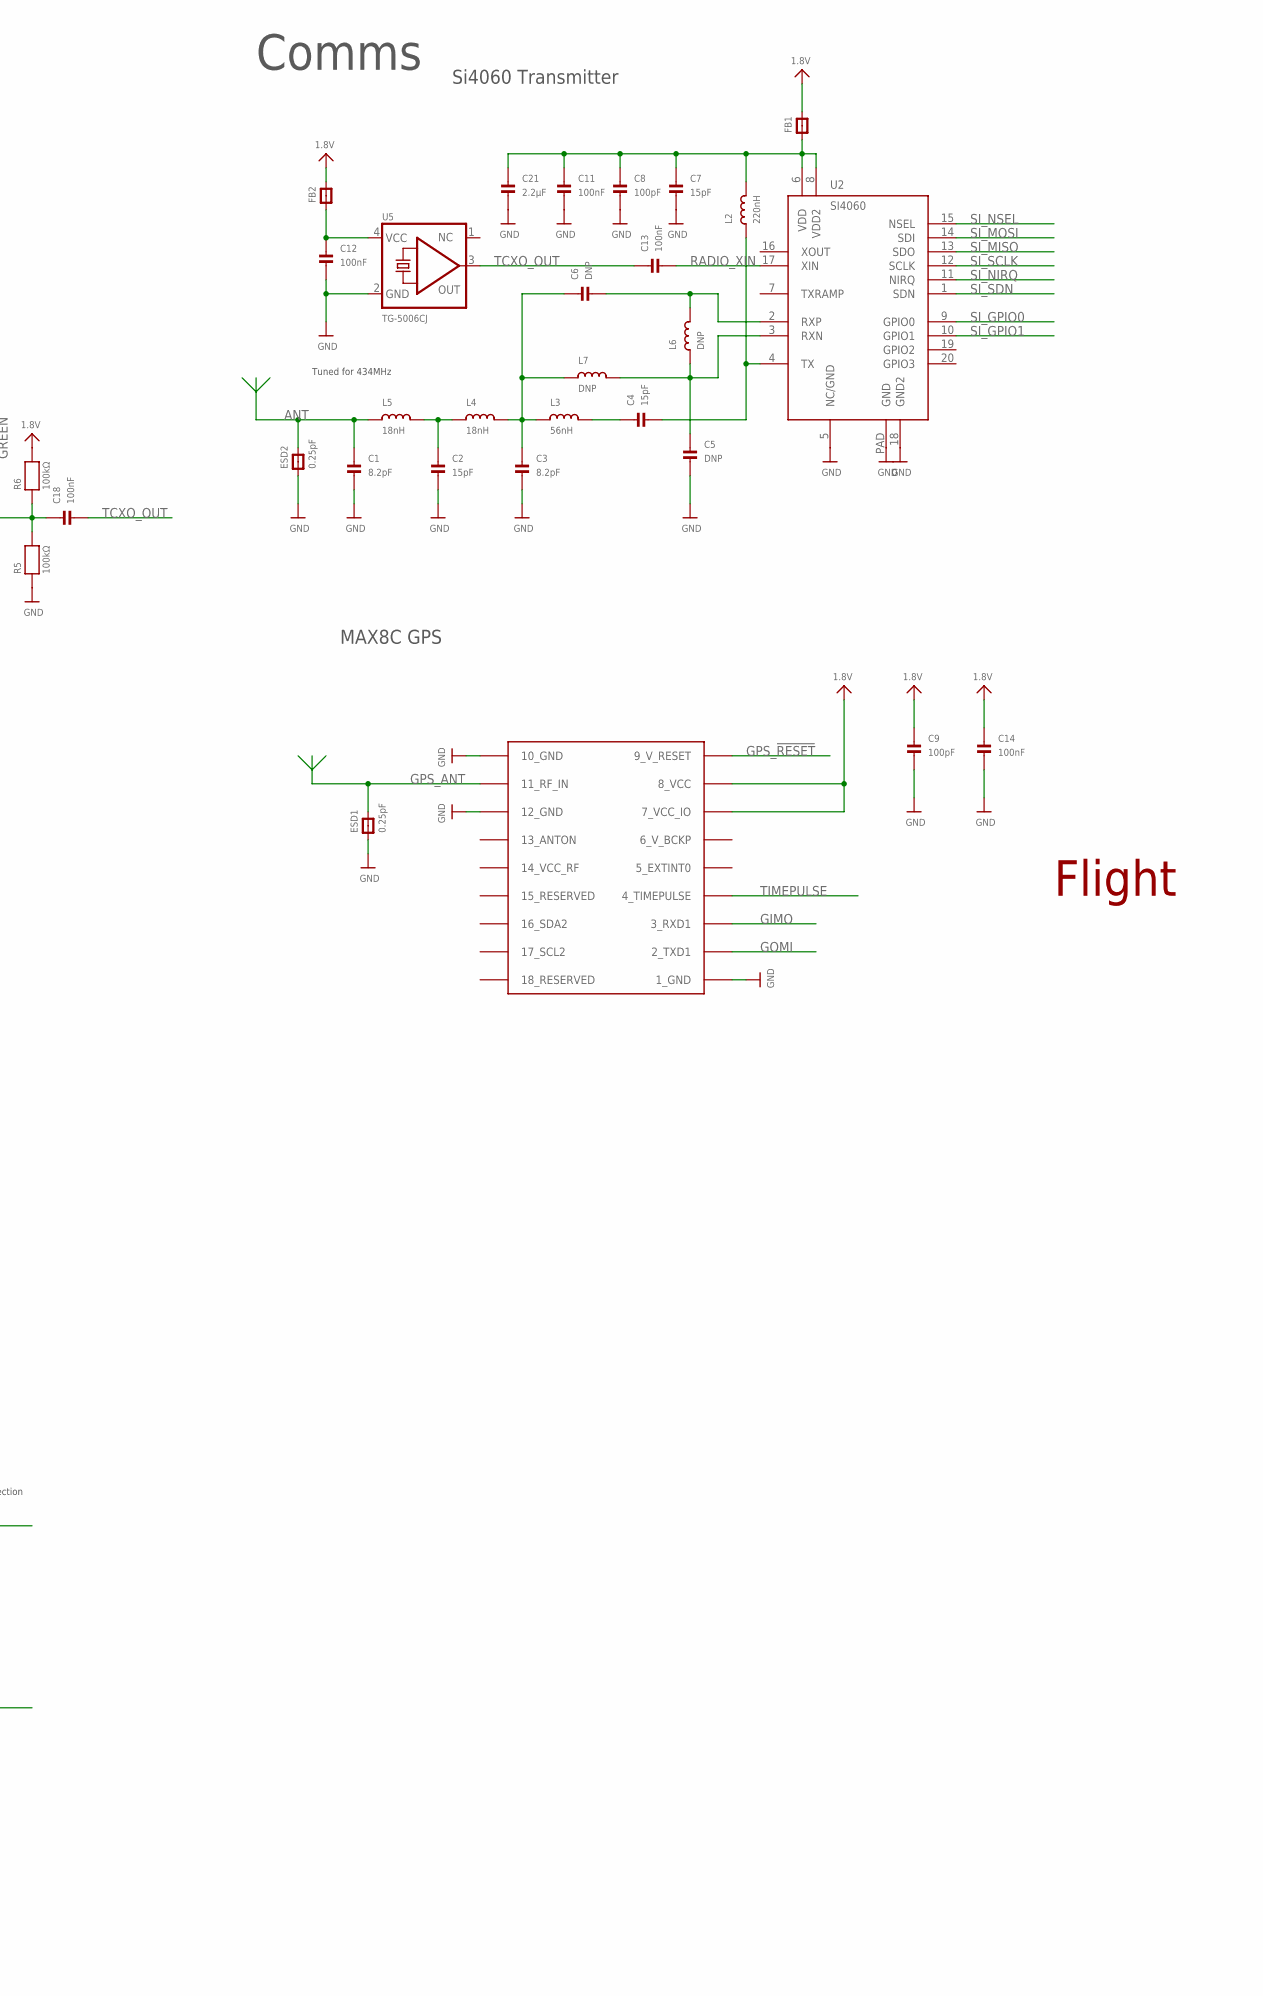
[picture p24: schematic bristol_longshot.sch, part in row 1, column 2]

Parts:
C1, C3: 8.2pF; _0402@1
C2, C4, C7: 15pF; _0402@1
C5, C6: DNP; _0402@1
C8, C9, C10: 100pF; _0402@1
C11, C12, C13, C14, C15, C16, C17, C18, C19: 100nF; _0402@1
C20: 1µF; _0402@1
C21: 2.2µF; _0402@1
C22, C23: 4.7µF; _0402@1
C24, C25: 10µF; C0603K
D1, D2, D3, D4, D5: RB161M
ESD1, ESD2: 0.25pF; _0603MP
FB1, FB2: FERRITE_0402; _0402@1
JTAG1: JTAG-CORTEXM3SMT; 2X05_1.27MM_SMT
L1: 10uH LPS3015; LPS3015
L2: 220nH; _0402@1
L3: 56nH; _0402@1
L4, L5: 18nH; _0402@1
L6, L7: DNP; _0402@1
LED1: GREEN; CHIPLED_0603
R1, R2, R3: 10kΩ; _0402
R4, R5, R6: 100kΩ; _0402
R7: 0Ω; _0402
R8: DNP; _0402
R10, R12, R14: 82kΩ; _0402
R11: 68kΩ; _0402
R13: 56kΩ; _0402
SJ1: SOLDERJUMPERREFLOW; SOLDERJUMPER_REFLOW
U1: SAM_D20E; QFN32_5MM
U2: SI4060; QFN20
U3: UBLOX_MAX
U4: SST25WF040BT-40I/NP; USON-8
U5: TG-5006CJ; TC-5006CJ
U6: LTC3105EDDPBF; DFN300X300X80-11N
U7: TPS3123; SOT23-5
U8: SN74LVC1G32DCKR; SOT65P210X110-5N
U9: MS5607-02BA03

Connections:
1.8V: C9.1, C10.1, C14.1, C15.1, C17.1, C19.1, C22.1, C25.1, FB1.2, FB2.2, JTAG1.1, LED1.A, R2.2, R3.2, R6.2, R11.2, U1.9 (VDD_ANA), U1.30 (VDD), U3.7_VCC_IO, U3.8_VCC, U4.7 (!HOLD), U4.8 (VDD), U6.9 (VOUT), U7.3 (!MR), U7.5 (VDD), U8.5 (VCC), U9.1 (VDD), U9.2 (PS)
!RESET: U1.26 (RESETN), U8.4 (Y)
ANT: C1.1, ESD2.2, L5.1
EXT!RESET: JTAG1.10, R1.2, U8.1 (A)
EXT_THERMISTOR_SENSE: R4.2, U1.4 (PA03)
FILTER1: C3.1, C6.1, L3.1, L4.2, L7.1
FILTER2: C2.1, L4.1, L5.2
GIMO: U1.7 (PA06), U3.3_RXD1
GND: C1.2, C2.2, C3.2, C5.2, C7.2, C8.2, C9.2, C10.2, C11.2, C12.2, C14.2, C15.2, C16.2, C17.2, C19.2, C20.2, C21.2, C22.2, C23.2, C24.2, C25.2, ESD1.1, ESD2.1, JTAG1.3, JTAG1.5, R1.1, R4.1, R5.1, R7.1, R10.1, R12.1, R14.1, U1.10 (GND1), U1.28 (GND2), U1.33 (GND), U2.5 (NC/GND), U2.18 (GND2), U2.PAD (GND), U3.1_GND, U3.10_GND, U3.12_GND, U4.4 (VSS), U4.P$9 (GND_PAD), U5.2 (GND), U6.11 (GND), U7.2 (GND), U8.3 (GND), U9.3 (GND), U9.4 (CSB1), U9.5 (CSB2)
GOMI: U1.8 (PA07), U3.2_TXD1
GPS_!RESET: U1.16 (PA15), U3.9_V_RESET
GPS_ANT: ESD1.2, U3.11_RF_IN
LED1: LED1.C, U1.17 (PA16)
MEM_CSN: U1.13 (PA10), U4.1 (!CE)
MEM_MISO: U1.14 (PA11), U4.2 (SO/SIO1)
MEM_MOSI: U1.11 (PA08), U4.5 (SI/SIO0)
MEM_SCK: U1.12 (PA09), U4.6 (SCK)
MEM_WPN: U4.3 (!WP)
MPPT_AUX: C20.1, U6.10 (AUX)
MPPT_FB: R11.1, R12.2, U6.1 (FB)
MPPT_FBLDO: R13.1, R14.2, U6.3 (FBLDO)
MPPT_LDO: C23.1, R13.2, U6.2 (LDO)
MPPT_SET: R8.2, R10.2, U6.5 (MPPC)
MPPT_SW: L1.2_1 (2), L1.2_2 (2), L1.2_3 (2), L1.2_4 (2), L1.2_5 (2), L1.2_6 (2), L1.2_7 (2), L1.2_8 (2), L1.2_9 (2), U6.7 (SW)
PANEL_1: D1.ANODE (A)
PANEL_2: D2.ANODE (A)
PANEL_3: D3.ANODE (A)
PANEL_4: D4.ANODE (A)
PRIMARY_AAA: D5.ANODE (A), SJ1.2
PRIMARY_AAA_CONTACT: SJ1.1
RADIO_VDD: C7.1, C8.1, C11.1, C21.1, FB1.1, L2.2, U2.6 (VDD), U2.8 (VDD2)
RADIO_XIN: C13.2, U2.17 (XIN)
RF_OUT: C4.2, L2.1, U2.4 (TX)
RF_TANK: C4.1, L3.2
RXN: C5.1, L6.1, L7.2, U2.3 (RXN)
RXP: C6.2, L6.2, U2.2 (RXP)
SAM_XOSC: C18.1, R5.2, R6.1, U1.15 (PA14)
SCL: R3.1, U1.2 (PA01), U9.8 (SCLK)
SDA: R2.1, U1.1 (PA00), U9.7 (SDI/SDA)
SI_GPIO0: U1.25 (PA27), U2.9 (GPIO0)
SI_GPIO1: U1.24 (PA25), U2.10 (GPIO1)
SI_MISO: U1.21 (PA22), U2.13 (SDO)
SI_MOSI: U1.20 (PA19), U2.14 (SDI)
SI_NIRQ: U1.23 (PA24), U2.11 (NIRQ)
SI_NSEL: U1.19 (PA18), U2.15 (NSEL)
SI_SCLK: U1.22 (PA23), U2.12 (SCLK)
SI_SDN: U1.18 (PA17), U2.1 (SDN)
SOLAR: C24.1, D1.CATHODE (C), D2.CATHODE (C), D3.CATHODE (C), D4.CATHODE (C), D5.CATHODE (C), L1.1_1 (1), L1.1_2 (1), L1.1_3 (1), L1.1_4 (1), L1.1_5 (1), L1.1_6 (1), L1.1_7 (1), L1.1_8 (1), L1.1_9 (1), R8.1, U1.5 (PA04), U6.6 (VIN)
SOLAR_MID: R7.2
SWDCLK: JTAG1.4, U1.31 (PA30/SWCLK)
SWDIO: JTAG1.2, U1.32 (PA31/SWDIO)
TCXO_OUT: C13.1, C18.2, U5.3 (OUT)
TCXO_VDD: C12.1, FB2.1, U5.4 (VCC)
TIMEPULSE: U1.6 (PA05), U3.4_TIMEPULSE
VDD_CORE: C16.1, U1.29 (VDD_CORE)
WDI: U1.27 (PA28), U7.4 (WDI)
WDI!RESET: U7.1 (!RESET), U8.2 (B)

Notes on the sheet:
ARM Cortex M0+: Atmel SAM D20E
(SERCOM3)
(SWD)
(EXTINT[12])
(DO: PAD3, SCK: PAD1)
(DOPO: 0x2)
(SERCOM2)
(DO: PAD0, SCK: PAD1, DOPO: 0x0)
(SERCOM0)
(TX: PAD2, TXPO: 0x1)
SST25WF04 4 MBit SPI Flash
Variant is S25FS128SAGNFI101
MAX8C GPS
Si4060 Transmitter
Tuned for 434MHz
CPU + Mem
Comms
Flight
(EXTINT[5])
(0.8V p-p min)
(AIN[1])
(AIN[4])
(SERCOM1)
!SHDN! is pulled high internally, so converter is always enabled
MPPT set point is 0.82V
1.1V - 1.3V expected from two series solar cells at 0ºC to -25ºC
Vf = 300mV @ -25ºC, 500mA
0.8V - 1V from solar array / primary lithium
MPPT output set to 1.85V
LDO output is set to 1.7V. Must be less that Vout.
1.2V - 1.4V expected from primary lithium AAA at 0ºC to -25ºC
This net is GND by default, but may be disconnected to form a solar midpoint connection
LTC3105 Boost Converter
MS5607 Pressure Sensor
Power + Sensor
Populate R8 with 0Ω resistor if SOLAR is connected directly to battery

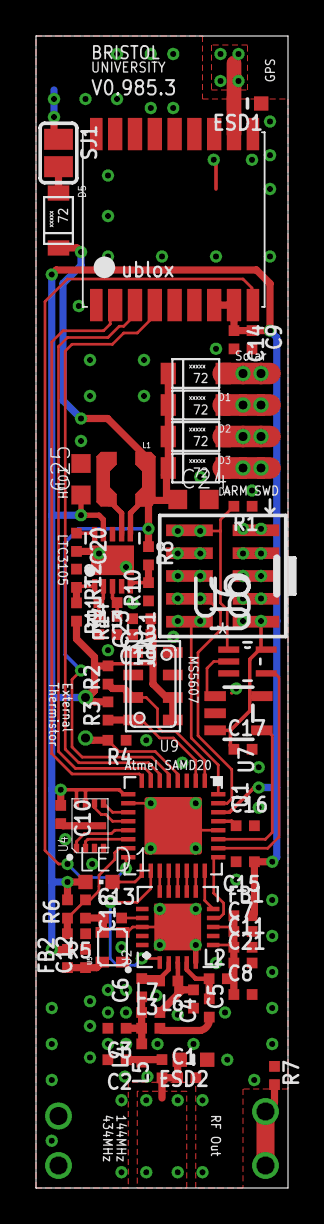
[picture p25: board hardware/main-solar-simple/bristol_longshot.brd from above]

Board: 2 copper layers, 14.0 x 64.0 mm, 66 parts (0 on the bottom side), 50 nets.

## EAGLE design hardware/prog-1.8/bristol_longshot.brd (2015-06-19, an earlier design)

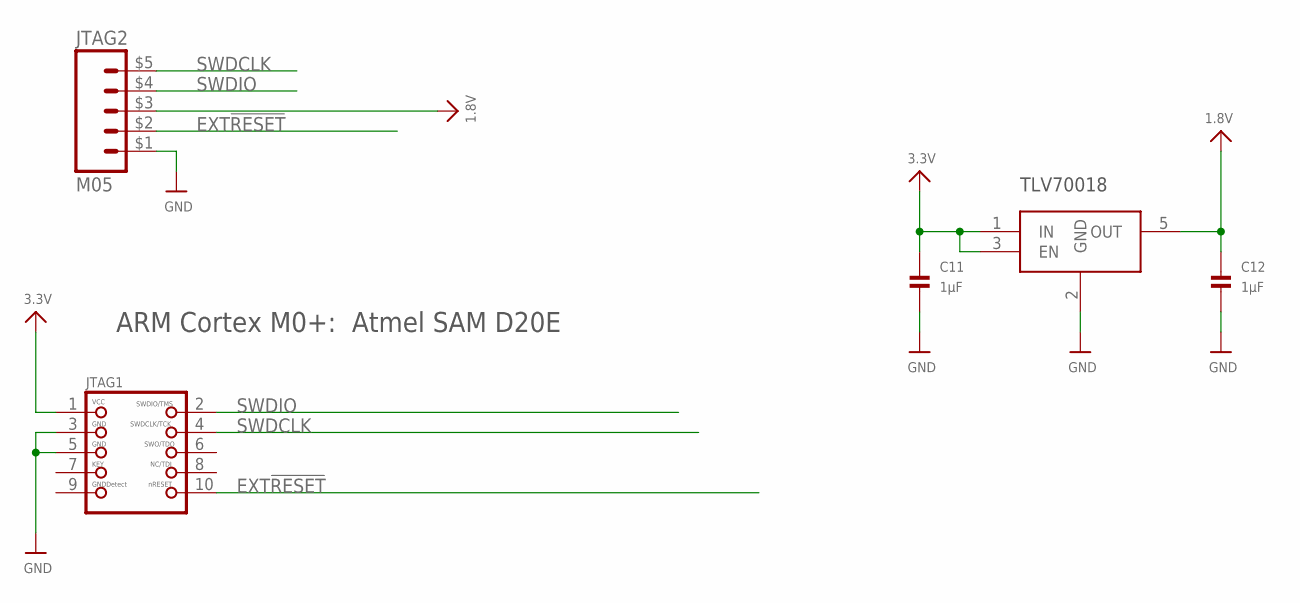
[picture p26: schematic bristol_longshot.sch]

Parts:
C11, C12: 1µF; _0402
JTAG1: JTAG-CORTEXM3SMT; 2X05_1.27MM_SMT
JTAG2: M05; M05_SIDE
U1: TLV70018DCK; SC70-5L

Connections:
1.8V: C12.1, JTAG2.$3 (3), U1.5 (OUT)
3.3V: C11.1, JTAG1.1, U1.1 (IN), U1.3 (EN)
EXT!RESET: JTAG1.10, JTAG2.$2 (2)
GND: C11.2, C12.2, JTAG1.3, JTAG1.5, JTAG2.$1 (1), U1.2 (GND)
SWDCLK: JTAG1.4, JTAG2.$5 (5)
SWDIO: JTAG1.2, JTAG2.$4 (4)

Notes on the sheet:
ARM Cortex M0+: Atmel SAM D20E
TLV70018

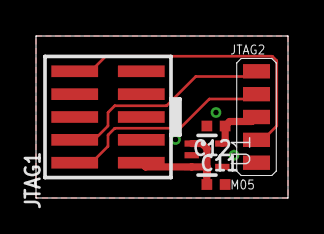
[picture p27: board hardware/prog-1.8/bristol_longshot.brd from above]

Board: 2 copper layers, 14.0 x 9.0 mm, 5 parts (0 on the bottom side), 6 nets.

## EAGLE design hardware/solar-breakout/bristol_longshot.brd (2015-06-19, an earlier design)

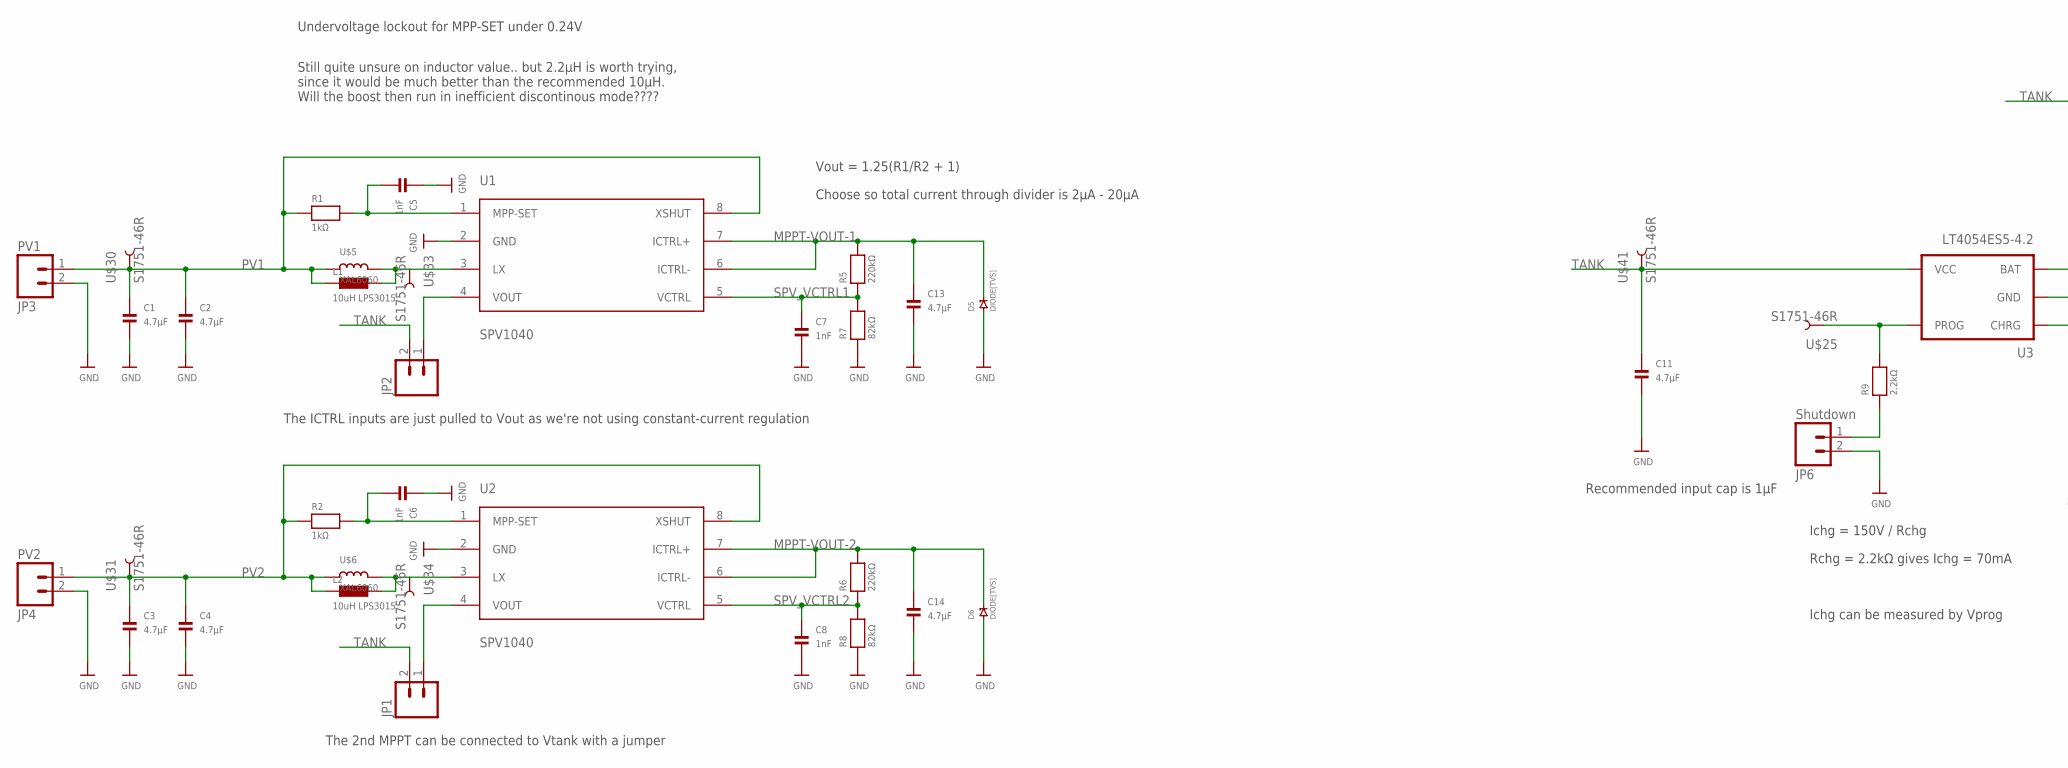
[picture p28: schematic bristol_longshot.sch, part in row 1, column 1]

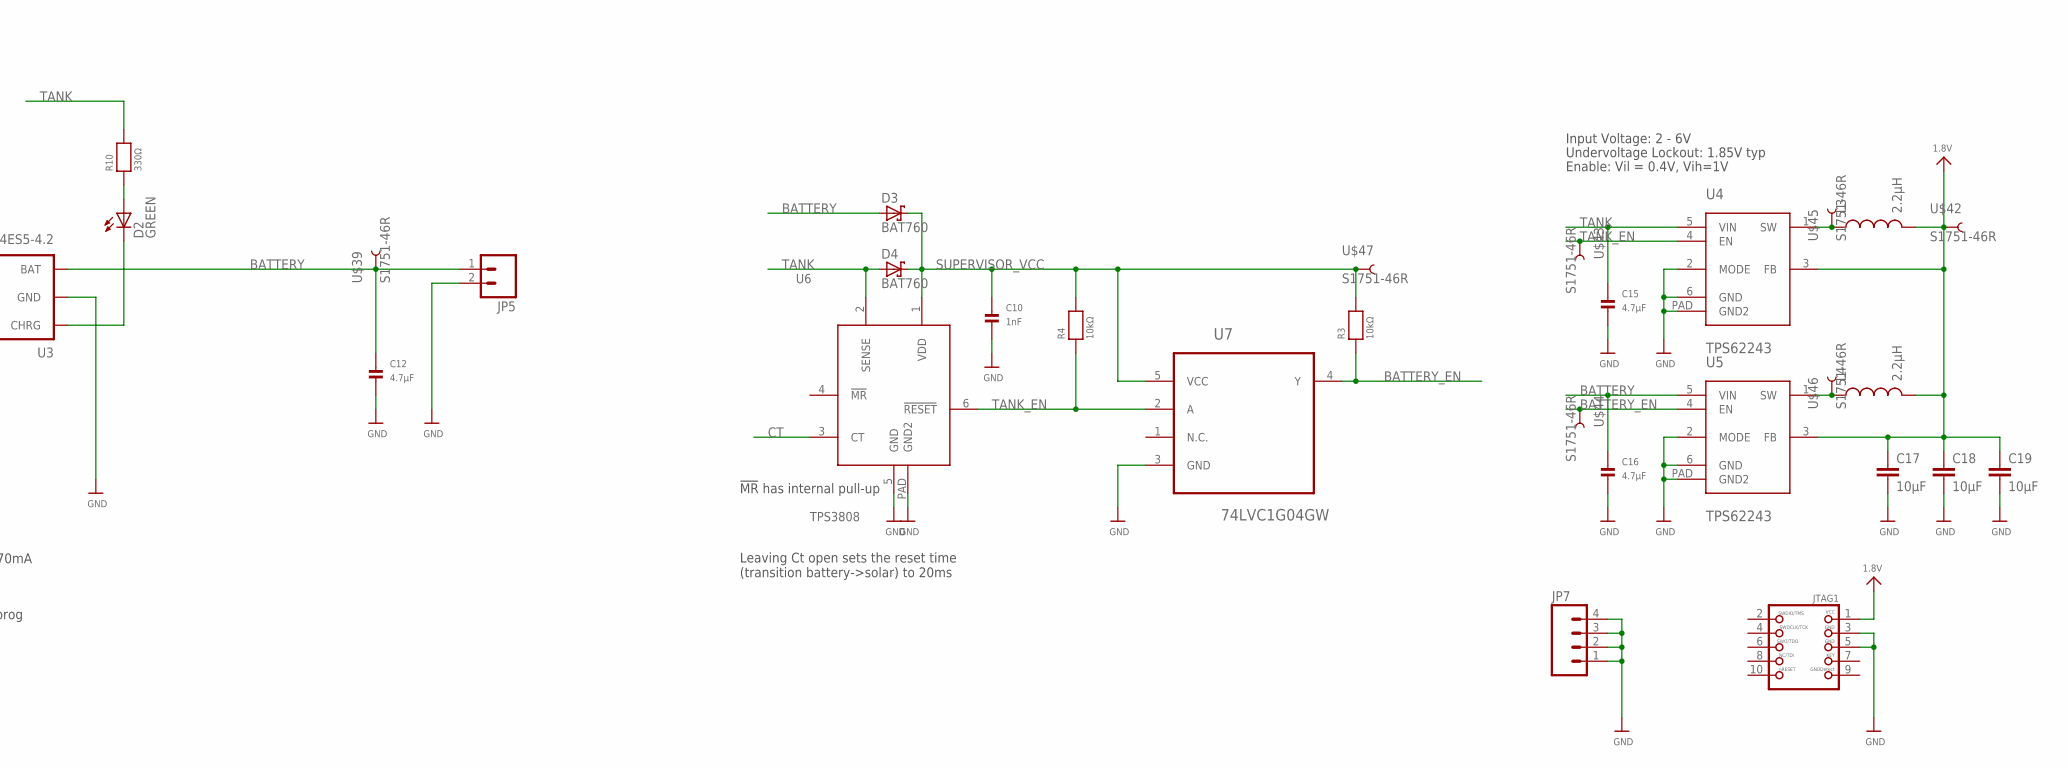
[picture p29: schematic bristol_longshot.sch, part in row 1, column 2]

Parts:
C1, C2, C3, C4, C11, C12, C13, C14, C15, C16: 4.7µF; _0402
C5, C6, C7, C8, C10: 1nF; _0402
C17, C18, C19: 10µF; C0603K
D2: GREEN; CHIPLED_0603
D3, D4: BAT760; SOD323
D5, D6: DIODE[TVS]; SOD123W
JP1, JP2: M02LOCK; 1X02_LOCK
JP3: PV1; SCREWTERMINAL-3.5MM-2_LOCK
JP4: PV2; SCREWTERMINAL-3.5MM-2_LOCK
JP5: M023.5MM_LOCK; SCREWTERMINAL-3.5MM-2_LOCK
JP6: Shutdown; 1X02_LOCK
JP7: M04LOCK; 1X04_LOCK
JTAG1: JTAG-CORTEXM3SMT; 2X05_1.27MM_SMT
L1, L2: 10uH LPS3015; LPS3015
L3, L4: 2.2µH; 1007
R1, R2: 1kΩ; _0402
R3, R4: 10kΩ; _0402
R5, R6: 220kΩ; _0402
R7, R8: 82kΩ; _0402
R9: 2.2kΩ; _0402
R10: 330Ω; _0402
U1, U2: SPV1040; TSSOP8
U3: LT4054ES5-4.2; SOT23-5
U4, U5: TPS62243; S-PWSON-N6
U6: TPS3808; S-PWSON-N6
U7: 74LVC1G04GW; SOT65P210X110-5N
U$5, U$6: XAL6060; XAL60
U$25, U$30, U$31, U$33, U$34, U$39, U$41, U$42, U$43, U$44, U$45, U$46, U$47: S1751-46R

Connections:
1.8V: C17.1, C18.1, C19.1, JTAG1.1, L3.2, L4.2, U4.3 (FB), U5.3 (FB), U$42.PAD
BATTERY: C12.1, C16.1, D3.A, JP5.1, U3.3 (BAT), U5.5 (VIN), U$39.PAD
BATTERY_BUCK_SW: L4.1, U5.1 (SW), U$46.PAD
BATTERY_EN: R3.1, U5.4 (EN), U7.4 (Y), U$44.PAD
CHG: D2.C, U3.1 (CHRG)
CHG_LED: D2.A, R10.1
CT: U6.3 (CT)
GND: C1.2, C2.2, C3.2, C4.2, C5.1, C6.1, C7.2, C8.2, C10.2, C11.2, C12.2, C13.2, C14.2, C15.2, C16.2, C17.2, C18.2, C19.2, D5.P$1 (1), D6.P$1 (1), JP3.2, JP4.2, JP5.2, JP6.2, JP7.1, JP7.2, JP7.3, JP7.4, JTAG1.3, JTAG1.5, R7.1, R8.1, U1.2 (GND), U2.2 (GND), U3.2 (GND), U4.2 (MODE), U4.6 (GND), U4.PAD (GND2), U5.2 (MODE), U5.6 (GND), U5.PAD (GND2), U6.5 (GND), U6.PAD (GND2), U7.3 (GND)
LX1: L1.2_1 (2), L1.2_2 (2), L1.2_3 (2), L1.2_4 (2), L1.2_5 (2), L1.2_6 (2), L1.2_7 (2), L1.2_8 (2), L1.2_9 (2), U1.3 (LX), U$5.P$2 (2), U$33.PAD
LX2: L2.2_1 (2), L2.2_2 (2), L2.2_3 (2), L2.2_4 (2), L2.2_5 (2), L2.2_6 (2), L2.2_7 (2), L2.2_8 (2), L2.2_9 (2), U2.3 (LX), U$6.P$2 (2), U$34.PAD
MPP-SET2: C6.2, R2.2, U2.1 (MPP-SET)
MPPT-VOUT-1: C13.1, D5.P$2 (2), JP2.1, R5.2, U1.4 (VOUT), U1.6 (ICTRL-), U1.7 (ICTRL+)
MPPT-VOUT-2: C14.1, D6.P$2 (2), JP1.1, R6.2, U2.4 (VOUT), U2.6 (ICTRL-), U2.7 (ICTRL+)
unnamed: C5.2, R1.2, U1.1 (MPP-SET)
unnamed: JP6.1, R9.1
PROG: R9.2, U3.5 (PROG), U$25.PAD
PV1: C1.1, C2.1, JP3.1, L1.1_1 (1), L1.1_2 (1), L1.1_3 (1), L1.1_4 (1), L1.1_5 (1), L1.1_6 (1), L1.1_7 (1), L1.1_8 (1), L1.1_9 (1), R1.1, U1.8 (XSHUT), U$5.P$1 (1), U$30.PAD
PV2: C3.1, C4.1, JP4.1, L2.1_1 (1), L2.1_2 (1), L2.1_3 (1), L2.1_4 (1), L2.1_5 (1), L2.1_6 (1), L2.1_7 (1), L2.1_8 (1), L2.1_9 (1), R2.1, U2.8 (XSHUT), U$6.P$1 (1), U$31.PAD
SPV_VCTRL1: C7.1, R5.1, R7.2, U1.5 (VCTRL)
SPV_VCTRL2: C8.1, R6.1, R8.2, U2.5 (VCTRL)
SUPERVISOR_VCC: C10.1, D3.C, D4.C, R3.2, R4.2, U6.1 (VDD), U7.5 (VCC), U$47.PAD
TANK: C11.1, C15.1, D4.A, JP1.2, JP2.2, R10.2, U3.4 (VCC), U4.5 (VIN), U6.2 (SENSE), U$41.PAD
TANK_BUCK_SW: L3.1, U4.1 (SW), U$45.PAD
TANK_EN: R4.1, U4.4 (EN), U6.6 (!RESET), U7.2 (A), U$43.PAD

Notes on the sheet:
Input Voltage: 2 - 6V
Enable: Vil = 0.4V, Vih=1V
Undervoltage Lockout: 1.85V typ
Undervoltage lockout for MPP-SET under 0.24V
Still quite unsure on inductor value.. but 2.2µH is worth trying, since it would be much better than the recommended 10µH. Will the boost then run in inefficient discontinous mode????
The 2nd MPPT can be connected to Vtank with a jumper
The ICTRL inputs are just pulled to Vout as we're not using constant-current regulation
Leaving Ct open sets the reset time (transition battery->solar) to 20ms
Recommended input cap is 1µF
Ichg = 150V / Rchg
!MR! has internal pull-up
Rchg = 2.2kΩ gives Ichg = 70mA
Ichg can be measured by Vprog
Vout = 1.25(R1/R2 + 1)
Choose so total current through divider is 2µA - 20µA

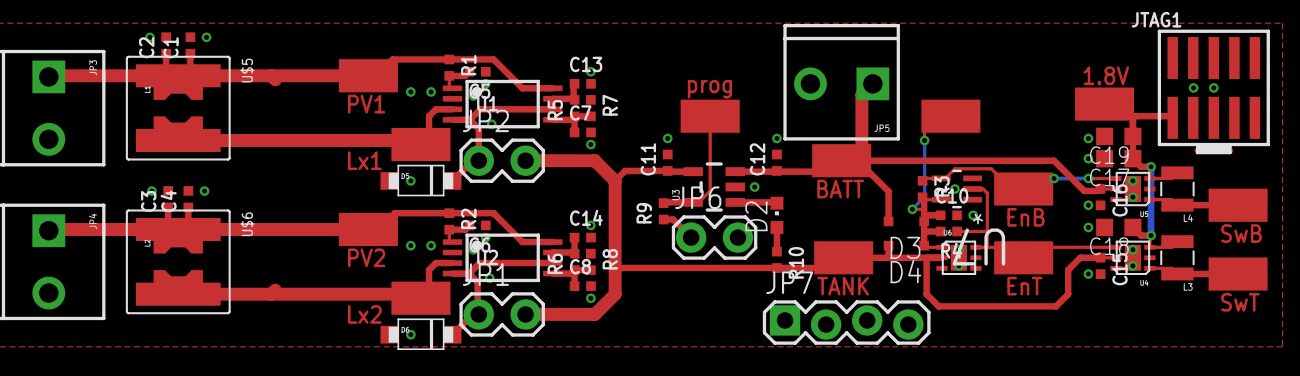
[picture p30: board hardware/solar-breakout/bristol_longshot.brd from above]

Board: 2 copper layers, 67 parts (0 on the bottom side), 23 nets.

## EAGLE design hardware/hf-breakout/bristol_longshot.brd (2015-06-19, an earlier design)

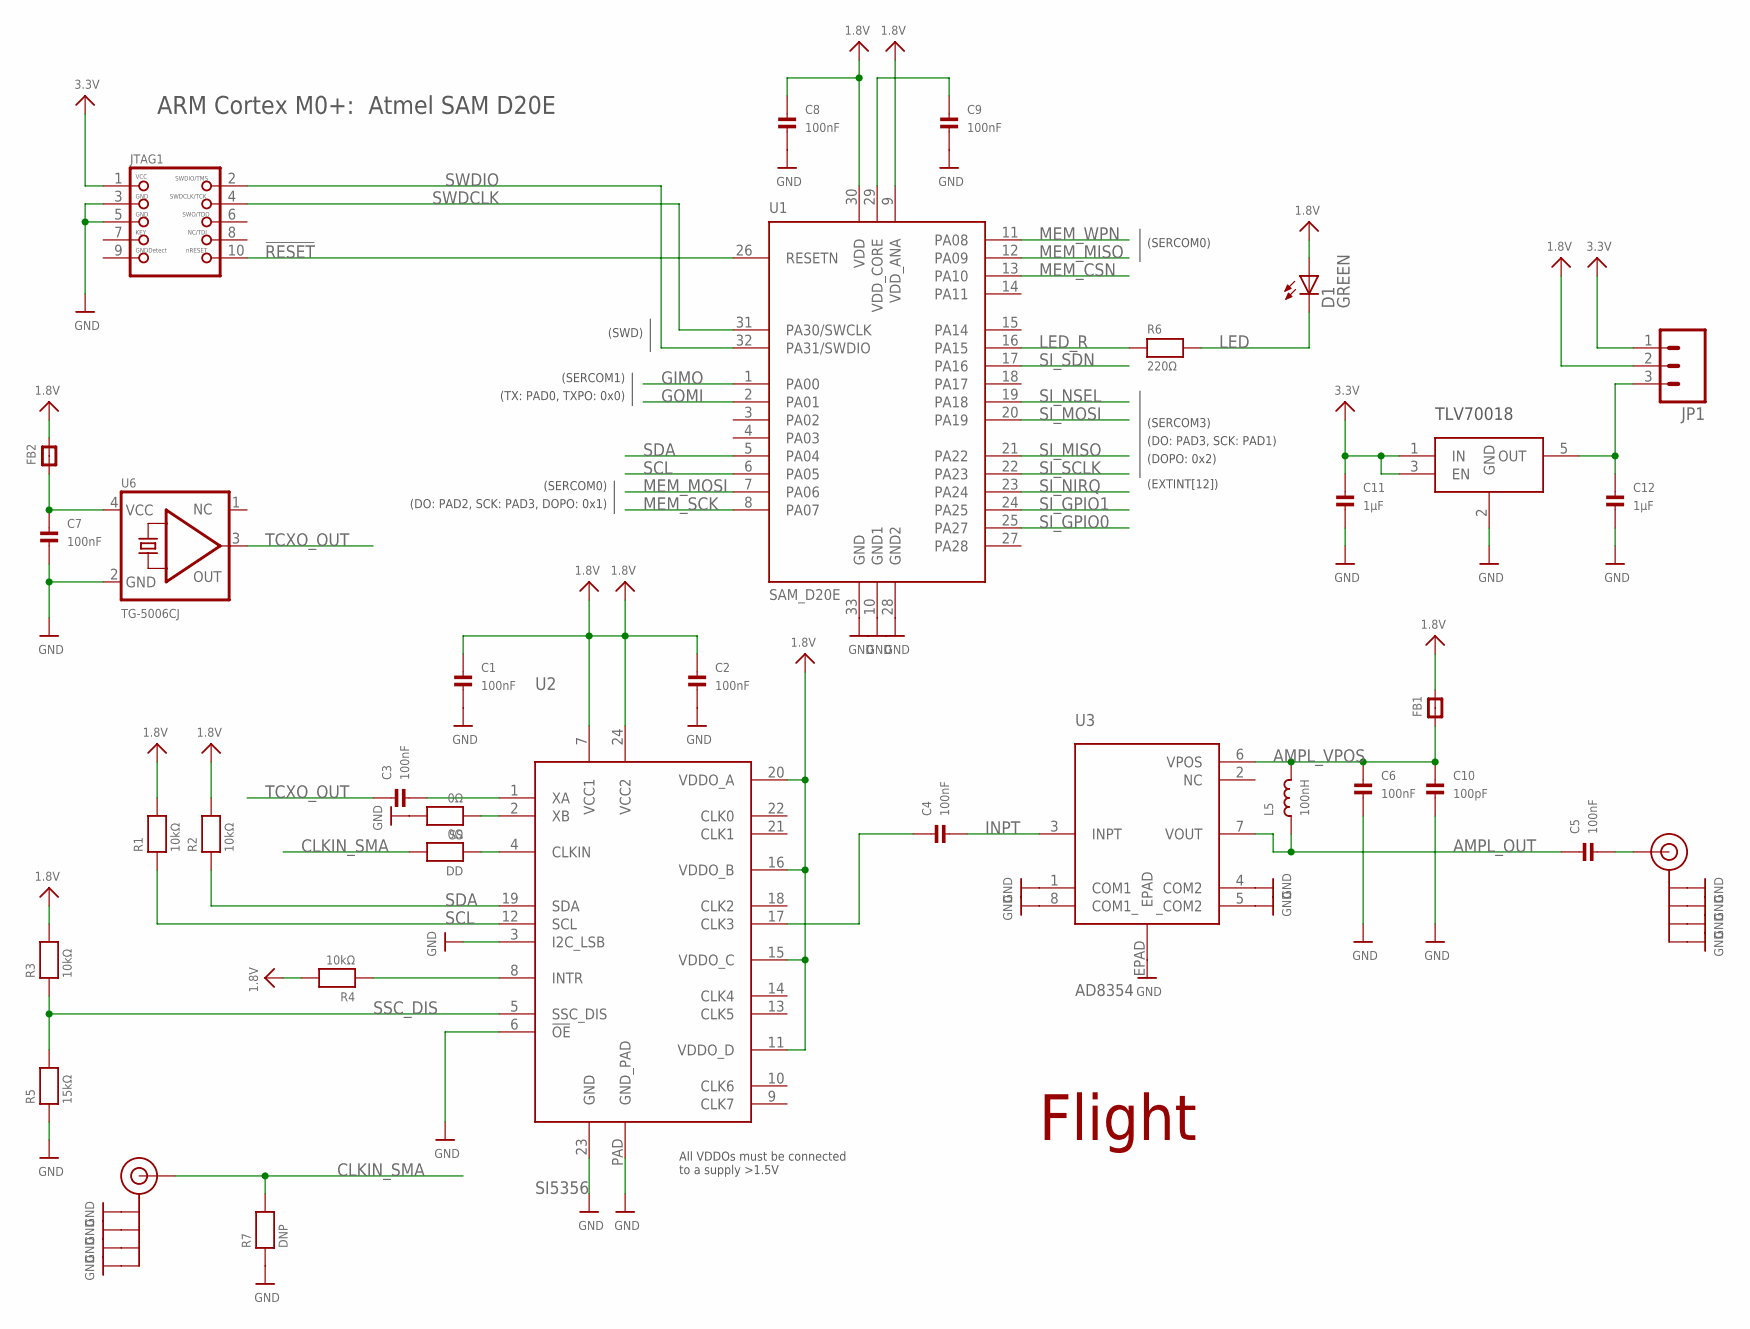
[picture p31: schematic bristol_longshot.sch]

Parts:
C1, C2, C3, C4, C5, C6, C7, C8, C9: 100nF; _0402
C10: 100pF; _0402
C11, C12: 1µF; _0402
D1: GREEN; CHIPLED_0603
DD: 0Ω; _0402
FB1, FB2: FERRITE_0402; _0402
J$1, J$2: SMA_EDGE; SMA-EDGE
JP1: M03LOCK; 1X03_LOCK
JTAG1: JTAG-CORTEXM3SMT; 2X05_1.27MM_SMT
L5: 100nH; _0402
R1, R2, R3, R4: 10kΩ; _0402
R5: 15kΩ; _0402
R6: 220Ω; _0402
R7: DNP; _0402
SS: 0Ω; _0402
U1: SAM_D20E; QFN32_5MM
U2: SI5356; QFN24_4MM
U3: AD8354; LFCSP_VD_8
U4: TLV70018DCK; SC70-5L
U6: TG-5006CJ; TC-5006CJ

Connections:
1.8V: C1.1, C2.1, C8.1, D1.A, FB1.2, FB2.2, JP1.2, R1.2, R2.2, R3.2, R4.2, U1.9 (VDD_ANA), U1.30 (VDD), U2.7 (VCC1), U2.11 (VDDO_D), U2.15 (VDDO_C), U2.16 (VDDO_B), U2.20 (VDDO_A), U2.24 (VCC2)
3.3V: C11.1, JP1.1, JTAG1.1, U4.1 (IN), U4.3 (EN)
!RESET: JTAG1.10, U1.26 (RESETN)
AMPL_OUT: C5.1, L5.1, U3.7 (VOUT)
AMPL_VPOS: C6.1, C10.1, FB1.1, L5.2, U3.6 (VPOS)
CLKIN: DD.1, U2.4 (CLKIN)
CLKIN_SMA: DD.2, J$1.SIG (SIGNAL), R7.2
GIMO: U1.1 (PA00)
GND: C1.2, C2.2, C6.2, C7.2, C8.2, C9.2, C10.2, C11.2, C12.2, J$1.GND@0 (GND), J$1.GND@1 (GND), J$1.GND@2 (GND), J$1.GND@3 (GND), J$2.GND@0 (GND), J$2.GND@1 (GND), J$2.GND@2 (GND), J$2.GND@3 (GND), JTAG1.3, JTAG1.5, R5.1, R7.1, SS.2, U1.10 (GND1), U1.28 (GND2), U1.33 (GND), U2.3 (I2C_LSB), U2.6 (!OE), U2.23 (GND), U2.PAD (GND_PAD), U3.1 (COM1), U3.4 (COM2), U3.5 (_COM2), U3.8 (COM1_), U3.EPAD, U4.2 (GND), U6.2 (GND)
GOMI: U1.2 (PA01)
HF: C5.2, J$2.SIG (SIGNAL)
HF_CLK: C4.1, U2.17 (CLK3)
INPT: C4.2, U3.3 (INPT)
INTR: R4.1, U2.8 (INTR)
LED: D1.C, R6.2
LED_R: R6.1, U1.16 (PA15)
MEM_CSN: U1.13 (PA10)
MEM_MISO: U1.12 (PA09)
MEM_MOSI: U1.7 (PA06)
MEM_SCK: U1.8 (PA07)
MEM_WPN: U1.11 (PA08)
unnamed: C12.1, JP1.3, U4.5 (OUT)
SCL: R1.1, U1.6 (PA05), U2.12 (SCL)
SDA: R2.1, U1.5 (PA04), U2.19 (SDA)
SI_GPIO0: U1.25 (PA27)
SI_GPIO1: U1.24 (PA25)
SI_MISO: U1.21 (PA22)
SI_MOSI: U1.20 (PA19)
SI_NIRQ: U1.23 (PA24)
SI_NSEL: U1.19 (PA18)
SI_SCLK: U1.22 (PA23)
SI_SDN: U1.17 (PA16)
SSC_DIS: R3.1, R5.2, U2.5 (SSC_DIS)
SWDCLK: JTAG1.4, U1.31 (PA30/SWCLK)
SWDIO: JTAG1.2, U1.32 (PA31/SWDIO)
TCXO_OUT: C3.1, U6.3 (OUT)
TCXO_VDD: C7.1, FB2.1, U6.4 (VCC)
VDD_CORE: C9.1, U1.29 (VDD_CORE)
XA: C3.2, U2.1 (XA)
XB: SS.1, U2.2 (XB)

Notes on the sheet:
ARM Cortex M0+: Atmel SAM D20E
(SERCOM3)
(SWD)
(SERCOM0)
(EXTINT[12])
(DO: PAD3, SCK: PAD1)
(DOPO: 0x2)
(DO: PAD2, SCK: PAD3, DOPO: 0x1)
(SERCOM1)
(TX: PAD0, TXPO: 0x0)
Flight
All VDDOs must be connected to a supply >1.5V
TLV70018


Board: 2 copper layers, 16.0 x 40.0 mm, 34 parts (0 on the bottom side), 25 nets.

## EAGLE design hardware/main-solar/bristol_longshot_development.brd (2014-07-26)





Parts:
BTN1: SPST.B3U-1000P(M)-B; B3U-1000P(M)-B
C1, C2, C3, C11, C12: 100nF; _0402
C4: 4.7µF; _0402
C5, C6: 2.2µF; _0402
C7, C9, C18: 15pF; _0402
C8, C10: 8.2pF; _0402
C13, C14, C15, C16, C17: 100pF; _0402
C19: 4.7µF; C0603K
C20, C21: 18pF; C0603K
C22, C23: 1µF; C0603K
C24, C25, C26: 100nF; C0603K
C27, C28, C29, C30: 10µF; C0603K
C31, C32: 100pF; C0603K
CN1: USBMINIB; USB-MINIB
D1, D3: GREEN; CHIPLED_0603
D2: RED; CHIPLED_0603
D4, D5: YELLOW; CHIPLED_0603
FB1: FERRITE_0402; _0402
IC1: V_REG_LM1117SOT223; SOT223
IC3: TLV70033DCK; SC70-5L
JP1, JP2, JP3, JP5, JP6, JP7, JP10, JP12, JP13, JP14, JP16: M02LOCK; 1X02_LOCK
JP4: M06LOCK; 1X06_LOCK
JP8, JP9: M05LOCK; 1X05_LOCK
JP11: M04LOCK; 1X04_LOCK
JTAG1, JTAG2: JTAG-CORTEXM3SMT; 2X05_1.27MM_SMT
L1: 3.3µH; 1007
L2: 220nH; _0402
L3: 56nH; _0402
L4, L5: 18nH; _0402
R1: 22Ω; _0402
R2, R3, R4: 1kΩ; _0402
R5, R6, R7, R8, R9, R10, R13, R14, R15, R16, R17, R18, R22, R23: 1Ω; _0402
R11, R29: 10K; 0603-MINI
R12, R19: 22Ω; 0603-MINI
R20: 4K7; 0603-MINI
R21: 1K5; 0603-MINI
R25, R26, R27, R28: 390Ω; 0603-MINI
U1: SAM_D20E; QFN32_5MM
U2: SI4060; QFN20
U3: MAX1947; TDFN8
U4: ANTENOVA_GPS_M10382
U5: S25FS-S; WSON8
U6: STM32F_48PIN; TQFP48
U7: LP38501TS-ADJ/NOPB; TO170P1435X457-6N
U$2, U$5, U$30, U$48, U$60, U$62, U$99: INA216; WCSP-4
Y1: 8MHz; CRYSTAL-SMD-5X3

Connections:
1.2V: U1.14 (PA11)
1.2VREG_OUT: C27.1, IC1.2 (OUT), IC1.4 (OUT), JP16.2
1.8V: D1.A, JP2.1, JP3.2, JP5.2, JP6.2, JP7.2, JTAG1.1, R7.1, R8.1, R9.2, R10.2, R13.2, R14.2, R15.2, R16.2, R17.2, R18.2, U6.18 (PB0), U$5.A2 (-), U$30.A1 (+), U$48.A1 (+), U$60.A1 (+), U$62.A1 (+)
3.3V: BTN1.2, C23.1, C24.1, C25.1, C26.1, IC3.5 (OUT), JP14.2, JTAG2.1, R26.1, U6.1 (VBAT), U6.9 (VDDA), U6.24 (VDD), U6.36 (VDD), U6.40 (PB4/JNTRST), U6.48 (VDD)
5.0V: C19.1, C22.1, C28.1, C31.1, CN1.VBUS, IC1.3 (IN), IC3.1 (IN), IC3.3 (EN), R20.2, U7.2 (IN)
ADJ_REG_EN: U7.1 (EN)
ADJ_REG_OUT: C29.1, C30.1, C32.1, JP13.2, U7.4 (OUT)
ADJ_REG_SWITCHING: U6.14 (PA4), U7.5 (ADJ)
ANT: C10.1, L5.1
AN_GPS_RX: C15.1, R4.1, U4.13_RX (RX)
AN_GPS_TX: R3.1, U4.11_TX (TX)
BOOT0: BTN1.1, R29.2, U6.44 (BOOT0)
D+: CN1.D+, R12.2, R21.2
D-: CN1.D-, R19.2
FILTER1: C8.1, L3.1, L4.2
FILTER2: C9.1, L4.1, L5.2
GND: C2.2, C3.2, C4.2, C5.2, C6.2, C8.2, C9.2, C10.2, C11.2, C12.2, C13.2, C14.2, C15.2, C16.2, C17.2, C18.2, C19.2, C20.1, C21.1, C22.2, C23.2, C24.2, C25.2, C26.2, C27.2, C28.2, C29.2, C30.2, C31.2, C32.2, CN1.GND, CN1.ID, D2.C, D3.C, D4.C, D5.C, IC1.1 (ADJ), IC3.2 (GND), JP4.1, JP8.1, JP9.1, JP10.1, JP11.1, JP12.1, JTAG1.3, JTAG1.5, JTAG2.3, JTAG2.5, R11.1, R29.1, U1.10 (GND1), U1.28 (GND2), U1.33 (GND), U2.5 (NC/GND), U2.18 (GND2), U2.PAD (GND), U3.2 (GNDA), U3.3 (GNDB), U3.5 (PGND), U3.PAD (GND_PAD), U4.2_GND (GND1), U4.4_GND (GND2), U4.14_GND (GND3), U4.17_GND (GND4), U4.21_GND (GND5), U4.24_GND (GND6), U4.26_GND (GND7), U4.28_GND (GND8), U4.32_VDD_USB (VDD_USB), U4.33_GND (GND9), U4.34_GND (GND10), U4.35_GND (GND11), U4.36_GND (GND12), U5.4 (VSS), U5.PAD (GND_PAD), U6.8 (VSSA), U6.23 (VSS), U6.35 (VSS), U6.47 (VSS), U7.3 (GND), U7.6 (DAP), U$2.B1 (GND), U$5.B1 (GND), U$30.B1 (GND), U$48.B1 (GND), U$60.B1 (GND), U$62.B1 (GND), U$99.B1 (GND)
GPS_ANT_IN: C1.2, U4.1_ANT_IN (ANT_IN)
GPS_ANT_OUT: C1.1, U4.3_ANT_OUT (ANT_OUT)
GPS_RX: JP11.3, R4.2, U1.1 (PA00)
GPS_TX: C16.1, JP11.4, R3.2, U1.2 (PA01)
I_PA: U6.12 (PA2), U$99.B2 (OUT)
I_STEPUP_IN: U6.16 (PA6), U$2.B2 (OUT)
I_STEPUP_OUT: U6.19 (PB1), U$5.B2 (OUT)
I_VDD_GPS: U6.15 (PA5), U$62.B2 (OUT)
I_VDD_MEM: U6.13 (PA3), U$48.B2 (OUT)
I_VDD_RADIO: U6.10 (PA0), U$60.B2 (OUT)
I_VDD_SAMD20: U6.11 (PA1), U$30.B2 (OUT)
LED0: R28.1, U6.20 (PB2/BOOT1)
LED1: R27.1, U6.21 (PB10)
LED2: R25.1, U6.22 (PB11)
LED_RES: D1.C, R1.2
LPC_XTAL2: C21.2, U6.6 (PD1/OSC_OUT), Y1.1
LX: L1.1, U3.6 (LX)
MEM_CSN: JP4.3, U1.13 (PA10), U5.1 (CSN)
MEM_MISO: JP4.5, U1.12 (PA09), U5.2 (SO/IO1)
MEM_MOSI: JP4.6, U1.7 (PA06), U5.5 (SI/IO0)
MEM_SCK: JP4.4, U1.8 (PA07), U5.6 (SCK)
MEM_WPN: JP4.2, U1.11 (PA08), U5.3 (WPN/IO2)
unnamed: D2.A, R25.2
unnamed: D3.A, R26.2
unnamed: D4.A, R27.2
unnamed: D5.A, R28.2
OSC_IN: C20.2, U6.5 (PD0/OSC_IN), Y1.3 (2)
RADIO_VDD: C6.1, C11.1, C17.1, C18.1, FB1.1, R22.2, R23.2, U2.6 (VDD), U2.8 (VDD2), U$99.A1 (+)
RESETN: JP12.2, JTAG1.10, U1.5 (PA04), U1.26 (RESETN), U3.1 (NRST)
RF_OUT: C7.2, L2.1, U2.4 (TX)
SI_GPIO0: JP9.2, R1.1, U1.25 (PA27), U2.9 (GPIO0)
SI_GPIO1: JP9.3, U1.24 (PA25), U2.10 (GPIO1)
SI_HF_CLK: JP10.2, U1.18 (PA17), U2.17 (XIN)
SI_MISO: JP8.4, U1.21 (PA22), U2.13 (SDO)
SI_MOSI: JP8.5, U1.20 (PA19), U2.14 (SDI)
SI_NIRQ: JP9.4, U1.23 (PA24), U2.11 (NIRQ)
SI_NSEL: JP8.2, U1.19 (PA18), U2.15 (NSEL)
SI_SCLK: JP8.3, U1.22 (PA23), U2.12 (SCLK)
SI_SDN: JP9.5, U1.17 (PA16), U2.1 (SDN)
STEPUP_IN: C5.1, C14.1, JP1.1, L1.2, R5.1, R6.1, U3.4 (NSHDN), U3.8 (BATT), U$2.A2 (-)
STEPUP_OUT: C4.1, JP2.2, R7.2, R8.2, U3.7 (OUT), U$5.A1 (+)
STM_SWDCLK: JTAG2.4, U6.37 (PA14/JTCK/SWCLK)
STM_SWDIO: JTAG2.2, U6.34 (PA13/JTMS)
SWDCLK: JTAG1.4, U1.31 (PA30/SWCLK)
SWDIO: JTAG1.2, U1.32 (PA31/SWDIO)
TANK: C7.1, L3.2
TIME_1KHZ: C13.1, JP11.2, R2.1, U1.27 (PA28)
TIME_1KHZ_DRIVE: R2.2, U4.23_TIMEPULSE/TDO (TIMEPULSE/TDO)
USB_DM: R19.1, U6.32 (PA11/USB_DM)
USB_DP: R12.1, U6.33 (PA12/USB_DP)
USB_ENUMERATE: R21.1, U6.29 (PA8)
VBUS: R11.2, R20.1, U6.26 (PB13)
VDD_CORE: C2.1, U1.29 (VDD_CORE)
VDD_GPS: JP7.1, R17.1, R18.1, U4.5_VIO (VIO), U4.25_VDD_RF (VDD_RF), U4.27_VCC (VCC), U$62.A2 (-)
VDD_MEM: C12.1, JP5.1, R13.1, R14.1, U5.8 (VDD), U$48.A2 (-)
VDD_PA: L2.2, R22.1, R23.1, U$99.A2 (-)
VDD_RADIO: FB1.2, JP6.1, R15.1, R16.1, U$60.A2 (-)
VDD_SAMD20: C3.1, JP3.1, R9.1, R10.1, U1.9 (VDD_ANA), U1.30 (VDD), U$30.A2 (-)
VDD_STEPUP: JP1.2, JP13.1, JP14.1, JP16.1, R5.2, R6.2, U6.17 (PA7), U$2.A1 (+)

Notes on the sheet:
ARM Cortex M0+: Atmel SAM D20E
(SERCOM3)
(SWD)
(GCLK_IO[0])
Using datasheet recomended values for 1-cell input, <2.7V output, <50% loading (ie. less than 400mA) Variant is MAX1947ETA18+T for 1.8V output. The inductor is a bourns CVH252009-3R3M with 0.1Ω ESR max in a 1008 package
(SERCOM0)
(EXTINT[12])
(DO: PAD3, SCK: PAD1)
(DOPO: 0x2)
(DO: PAD2, SCK: PAD3, DOPO: 0x1)
(GCLK_IO[3])
(SERCOM1)
(TX: PAD0, TXPO: 0x0)
MAX1947 Step-Up DC-DC Converter VBatt -> 1.8V
(AIN[19])
S25FS128 128 MBit SPI Flash
Variant is S25FS128SAGNFI101
Antenova M10382 GPS Module, U-Blox Chipset
Si4060 Transmitter
Tuned for 434MHz
CPU + Mem + Power
Comms
Development connectitons
Development
Current Sense
STM32F103CB
TLV70033
Busses
USB Interface
USB 5.0V
1.2V
ADJ
3.3V
STM
1.8V

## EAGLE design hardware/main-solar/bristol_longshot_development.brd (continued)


Board: 2 copper layers, 50.0 x 50.0 mm, 107 parts (0 on the bottom side), 74 nets.

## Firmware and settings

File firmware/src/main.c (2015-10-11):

/*
 * Bristol SEDS pico-tracker
 * Copyright (C) 2014  Richard Meadows <richardeoin>
 *
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
 * THE SOFTWARE IS PROVIDED "AS IS", WITHOUT WARRANTY OF ANY KIND,
 * EXPRESS OR IMPLIED, INCLUDING BUT NOT LIMITED TO THE WARRANTIES OF
 * MERCHANTABILITY, FITNESS FOR A PARTICULAR PURPOSE AND
 * NONINFRINGEMENT. IN NO EVENT SHALL THE AUTHORS OR COPYRIGHT HOLDERS BE
 * LIABLE FOR ANY CLAIM, DAMAGES OR OTHER LIABILITY, WHETHER IN AN ACTION
 * OF CONTRACT, TORT OR OTHERWISE, ARISING FROM, OUT OF OR IN CONNECTION
 * WITH THE SOFTWARE OR THE USE OR OTHER DEALINGS IN THE SOFTWARE.
 */

#include <stdio.h>
#include <math.h>
#include <string.h>

#include "samd20.h"
#include "hw_config.h"
#include "init.h"
#include "gps.h"
#include "mfsk.h"
#include "watchdog.h"
#include "telemetry.h"
#include "timer.h"
#include "contestia.h"
#include "aprs.h"
#include "location.h"
#include "rf_tests.h"
#include "data.h"
#include "backlog.h"
#include "pips.h"

#define CALLSIGN	"UBSEDS11"
#define APRS_COMMENT	"CONTESTIA/434.6"

/**
 * Formats a UKHAS telemetry string for the given datapoint
 *
 * The telemetry string starts with the specified number of dollar signs
 */
uint16_t format_telemetry_string(char* string, struct tracker_datapoint* dp,
                                 uint8_t dollars, uint8_t reduce_char_set)
{
  double lat_fmt = 0.0;
  double lon_fmt = 0.0;
  uint32_t altitude = 0;
  uint16_t len;

  lat_fmt = (double)dp->latitude / 10000000.0;  /* hundred nanodeg -> degrees */
  lon_fmt = (double)dp->longitude / 10000000.0; /* hundred nanodeg -> degrees */
  altitude = dp->altitude / 1000;               /* mm -> meters */

  /* sprintf - preamble */
  memset(string, '$', dollars);
  len = dollars;

  /* sprintf - full string (approx 90 chars) */
  len += sprintf(telemetry_string + len,
                 "%s,%02u:%02u:%02u,%02u%02u%02u,%02.5f,%03.5f,%ld,%u,%.2f,%ld,%.1f,%.1f,%.1f,%ld",
                 CALLSIGN,      /* 2+6+2+1=11 */
                 dp->time.hour, dp->time.minute, dp->time.second, /* 2+1+2+1+2+1=9 */
                 dp->time.year%100, dp->time.month, dp->time.day, /* 2+2+2+1=7 */
                 lat_fmt, lon_fmt, altitude, dp->satillite_count, /* 3+1+5+1 + 4+1+5+1 + 5+1 + 2+1 = 30 */
                 dp->solar, dp->main_pressure, /* 1+1+2+1 + 5+1 = 11 */
                 dp->thermistor_temperature, dp->bmp180_temperature, /* 3+1+1+1 + 3+1+1+1 = 12 */
                 dp->radio_die_temperature, dp->xosc_error); /* 3+1+1+1 + 4 = 10 */
                 /* sum = 90 (must be less than or equal to 114) */

  if (reduce_char_set) {
    /* Reduce character set */
    contestiaize(telemetry_string + dollars);
  }

  /* sprintf - checksum. don't include dollars */
  len += sprintf(telemetry_string + len,
		 "*%04X\r",
		 crc_checksum(telemetry_string + dollars));

  /* Length should be no more than 120 characters!! (24 seconds transmission time) */
  if (len <= 120) {
    return len;
  }

  /* Okay, let's use a shorter backup format */
  len = dollars;

  /* sprintf - short format */
  len += sprintf(telemetry_string + len,
                 "%s,%02u:%02u:%02u,%02.5f,%03.5f,%ld",
                 CALLSIGN,
                 dp->time.hour, dp->time.minute, dp->time.second,
                 lat_fmt, lon_fmt, altitude);

  if (reduce_char_set) {
    /* Reduce character set */
    contestiaize(telemetry_string + dollars);
  }

  /* sprintf - checksum. don't include dollars */
  len += sprintf(telemetry_string + len,
		 "*%04X\r",
		 crc_checksum(telemetry_string + dollars));

  return len;
}


/**
 * RTTY telemetry. Uses 5 dollar symbols
 */
#define RTTY_DOLLARS 5
void rtty_telemetry(struct tracker_datapoint* dp) {
  uint16_t len;

  len = format_telemetry_string(telemetry_string, dp, RTTY_DOLLARS, 0);

  /* Main telemetry */
  telemetry_start(TELEMETRY_RTTY, len);

  /* Sleep Wait for main telemetry */
  while (telemetry_active()) {
    idle(IDLE_TELEMETRY_ACTIVE);
  }
}
/**
 * Contestia telemetry. Uses 2 dollar symbols
 */
#define CONTESTIA_DOLLARS 2
void contestia_telemetry(struct tracker_datapoint* dp) {
  uint16_t len;

  len = format_telemetry_string(telemetry_string, dp, CONTESTIA_DOLLARS, 1);

  /* RSID */
  telemetry_start_rsid(RSID_CONTESTIA_32_1000);

  /* Sleep Wait for RSID */
  while (telemetry_active()) {
    idle(IDLE_TELEMETRY_ACTIVE);
  }

  /* Main telemetry */
  telemetry_start(TELEMETRY_CONTESTIA, len);

  /* Sleep Wait for main telemetry */
  while (telemetry_active()) {
    idle(IDLE_TELEMETRY_ACTIVE);
  }
}
/**
 * APRS telemetry if required
 */
void aprs_telemetry(struct tracker_datapoint* dp) {

  struct tracker_datapoint* backlog_dp_ptr;

  if (!gps_is_locked()) return; /* Don't bother with no GPS */

  /* Update location */
  aprs_location_update(dp->longitude, dp->latitude);

#if APRS_USE_GEOFENCE
  /* aprs okay here? */
  if (aprs_location_tx_allow()) {
#endif

    /* Set location */
    aprs_set_datapoint(dp);

    /* Set comment */
    if ((dp->time.minute % 4) == 0) {
      aprs_set_comment(APRS_COMMENT);
    } else {
      backlog_dp_ptr = get_backlog();

      if (backlog_dp_ptr != NULL) {     /* Backlog comment if we can */
        aprs_set_backlog_comment(backlog_dp_ptr);
      } else {
        aprs_set_comment(APRS_COMMENT);
      }
    }

    /* Set frequency */
#if APRS_USE_GEOFENCE
    telemetry_aprs_set_frequency(aprs_location_frequency());
#else
    telemetry_aprs_set_frequency(144800000);
#endif

    /* Transmit packet and wait */
    telemetry_start(TELEMETRY_APRS, 0xFFFF);
    while (telemetry_active()) {
      idle(IDLE_TELEMETRY_ACTIVE);
    }

#if APRS_USE_GEOFENCE
  }
#endif
}
/**
 * Pips telemetry
 */
void pips_telemetry(void)
{
  /* Pips */
  telemetry_start(TELEMETRY_PIPS, 0xFFFF);

  while (telemetry_active()) {
    idle(IDLE_TELEMETRY_ACTIVE);
  }
}

volatile uint8_t tick_flag = 0;

/**
 * Called at 1Hz by the GPS
 */
void gps_tick(uint32_t sequence)
{
  /* Sequence not used */
  (void)sequence;

  /* Update internal time representation */
  cron_tick();

  /* Raise the tick flag */
  tick_flag = 1;
}

/**
 * MAIN
 * =============================================================================
 */
int main(void)
{
  /* Init */
  init(gps_tick, INIT_NORMAL);

  /* Maybe do some rf tests */
  rf_tests();

  /* Turn off LED to show we've initialised correctly */
  led_off();

  while (1) {
    /* Run cron job */
    if (tick_flag) {
      tick_flag = 0; do_cron();
    }

    /* Idle */
    idle(IDLE_WAIT_FOR_NEXT_TELEMETRY);
  }
}

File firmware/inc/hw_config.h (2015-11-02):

/*
 * Hardware definitions and configuations
 * Copyright (C) 2014  Richard Meadows <richardeoin>
 *
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
 * THE SOFTWARE IS PROVIDED "AS IS", WITHOUT WARRANTY OF ANY KIND,
 * EXPRESS OR IMPLIED, INCLUDING BUT NOT LIMITED TO THE WARRANTIES OF
 * MERCHANTABILITY, FITNESS FOR A PARTICULAR PURPOSE AND
 * NONINFRINGEMENT. IN NO EVENT SHALL THE AUTHORS OR COPYRIGHT HOLDERS BE
 * LIABLE FOR ANY CLAIM, DAMAGES OR OTHER LIABILITY, WHETHER IN AN ACTION
 * OF CONTRACT, TORT OR OTHERWISE, ARISING FROM, OUT OF OR IN CONNECTION
 * WITH THE SOFTWARE OR THE USE OR OTHER DEALINGS IN THE SOFTWARE.
 */

#ifndef HW_CONFIG_H
#define HW_CONFIG_H

#include "port.h"
#include "samd20.h"
#include "adc/adc.h"

/*
 * Convenience definitions for available GPIO modules
 */
#if (PORT_GROUPS > 0)
#define PORTA		PORT->Group[0]
#endif
#if (PORT_GROUPS > 1)
#define PORTB		PORT->Group[1]
#endif
#if (PORT_GROUPS > 2)
#define PORTC		PORT->Group[2]
#endif
#if (PORT_GROUPS > 3)
#define PORTD		PORT->Group[3]
#endif


//#define XPLAINED

/**
 * LED
 */
#ifdef XPLAINED
#define LED0_PIN		PIN_PA14
#else
#define LED0_PIN		PIN_PA16
#endif

/**
 * GPS
 */
#define GPS_SERCOM		(SercomUsart*)SERCOM0
#define GPS_SERCOM_MOGI_PIN	PIN_PA06
#define GPS_SERCOM_MOGI_PINMUX	PINMUX_PA06D_SERCOM0_PAD2
#define GPS_SERCOM_MIGO_PIN	PIN_PA07
#define GPS_SERCOM_MIGO_PINMUX	PINMUX_PA07D_SERCOM0_PAD3
#define GPS_SERCOM_MUX		USART_RX_3_TX_2_XCK_3
#define GPS_GCLK		GCLK_GENERATOR_1
#define GPS_BAUD_RATE		9600
#define GPS_PLATFORM_MODEL	UBX_PLATFORM_MODEL_AIRBORNE_1G
#define GPS_TIMEPULSE_PIN	PIN_PA05
#define GPS_TIMEPULSE_PINMUX	PINMUX_PA05A_EIC_EXTINT5
#define GPS_TIMEPULSE_FREQ      1
#define GPS_TIMEPULSE_EXTINT	5
#define GPS_RESET_PIN		PIN_PA15

/**
 * USART Loopback Testing
 */
#define USART_MUX_LOOPBACK	USART_RX_2_TX_2_XCK_3

/**
 * Flash Memory
 */
#define FLASH_SERCOM		(SercomSpi*)SERCOM2
#define FLASH_SERCOM_MOSI_PIN	PIN_PA08
#define FLASH_SERCOM_MOSI_PINMUX PINMUX_PA08D_SERCOM2_PAD0
#define FLASH_SERCOM_MISO_PIN	PIN_PA11
#define FLASH_SERCOM_MISO_PINMUX PINMUX_PA11D_SERCOM2_PAD3
#define FLASH_SERCOM_SCK_PIN	PIN_PA09
#define FLASH_SERCOM_SCK_PINMUX PINMUX_PA09D_SERCOM2_PAD1
#define FLASH_SERCOM_MUX	SPI_SIGNAL_MUX_SETTING_D
#define FLASH_CSN_PIN		PIN_PA10

/**
 * I2C Bus
 */
#define I2C_SERCOM		(SercomI2cm*)SERCOM1
#define I2C_SERCOM_SDA_PIN	PIN_PA00
#define I2C_SERCOM_SDA_PINMUX	PINMUX_PA00D_SERCOM1_PAD0
#define I2C_SERCOM_SCL_PIN	PIN_PA01
#define I2C_SERCOM_SCL_PINMUX	PINMUX_PA01D_SERCOM1_PAD1

/**
 * Barometer
 */
#define BAROMETER_TYPE_BMP180 0
#define BAROMETER_TYPE_MS5607 1

/**
 * Battery ADC
 */
#define BATTERY_ADC		0
#define BATTERY_ADC_PIN		PIN_PA02
#define BATTERY_ADC_PINMUX	PINMUX_PA02B_ADC_AIN0
#define BATTERY_ADC_CHANNEL	ADC_POSITIVE_INPUT_PIN0
#define BATTERY_ADC_CHANNEL_DIV	0.3125

/**
 * External Thermistor ADC
 */
#define THERMISTOR_ADC		1
#define THERMISTOR_ADC_PIN	PIN_PA03
#define THERMISTOR_ADC_PINMUX	PINMUX_PA03
#define THERMISTOR_ADC_CHANNEL	ADC_POSITIVE_INPUT_PIN1
#define THERMISTOR_ADC_CHANNEL_DIV 1

/**
 * Solar ADC
 */
#define SOLAR_ADC		1
#define SOLAR_ADC_PIN		PIN_PA04
#define SOLAR_ADC_PINMUX	PINMUX_PA04B_ADC_AIN4
#define SOLAR_ADC_CHANNEL	ADC_POSITIVE_INPUT_PIN4
#define SOLAR_ADC_CHANNEL_DIV	1

/**
 * Radio
 */
#define SI4xxx_SERCOM		(SercomSpi*)SERCOM3
#define SI4xxx_SERCOM_MOSI_PIN	PIN_PA19
#define SI4xxx_SERCOM_MOSI_PINMUX PINMUX_PA19D_SERCOM3_PAD3
#define SI4xxx_SERCOM_MISO_PIN	PIN_PA22
#define SI4xxx_SERCOM_MISO_PINMUX PINMUX_PA22C_SERCOM3_PAD0
#define SI4xxx_SERCOM_SCK_PIN	PIN_PA23
#define SI4xxx_SERCOM_SCK_PINMUX	PINMUX_PA23C_SERCOM3_PAD1
#define SI4xxx_SERCOM_MUX	SPI_SIGNAL_MUX_SETTING_M
#define SI4xxx_SEL_PIN		PIN_PA18
#define SI4xxx_IRQ_PIN		PIN_PA24
#define SI4xxx_IRQ_PINMUX	PINMUX_PA24A_EIC_EXTINT12
#define SI4xxx_SDN_PIN		PIN_PA17
#define SI4xxx_GPIO0_PIN	PIN_PA27
#define SI4xxx_GPIO1_PIN	PIN_PA25
#define SI4xxx_GPIO1_PINMUX	PINMUX_PA25F_TC5_WO1
#define SI4xxx_TCXO_FREQUENCY	16369000

/**
 * RF Power @ 1.8V
 *
 * These values are taken from the datasheet, but the
 * difference between them has been measured as 6dB
 */
#define RF_POWER_14dBm		0x7f
#define RF_POWER_8dBm		36

/**
 * XOSC
 */
#define USE_XOSC		1
#define XOSC_FREQUENCY		16369000
#define XOSC_GCLK1_DIVIDE	2

/**
 * Telemetry
 */
#define TELEMETRY_FREQUENCY	434602000
#define TELEMETRY_POWER		RF_POWER_8dBm
#define TELEMETRY_USE_GEOFENCE	1

/**
 * APRS
 */
#define APRS_ENABLE		1
#define APRS_USE_GEOFENCE	1
#define APRS_POWER		RF_POWER_14dBm

/**
 * Watchdog Timer
 *
 * There is a performance penalty to using the watchdog - you must
 * wait up to 1/16kHz when kicking to sync with it. Disable when not in use
 */
#define DEBUG_USE_INTWATCHDOG	0
#define WDT_GCLK		GCLK_GENERATOR_4

/**
 * External Watchdog Timer
 */
#define WDT_WDI_PIN		PIN_PA28

/**
 * SWD
 */
#define SWD_SWDCLK_PIN		PIN_PA30
#define SWD_SWDCLK_PINMUX	PINMUX_PA30G_CORE_SWCLK
#define SWD_SWDIO_PIN		PIN_PA31


/**
 * Interrupt Priority
 */
#define WDT_INT_PRIO		0 /* Early warning interrupt */
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

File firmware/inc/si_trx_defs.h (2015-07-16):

/*
 * Definitions and macros for Si Labs Tranceivers
 * Copyright (C) 2014  Richard Meadows <richardeoin>
 *
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
 * THE SOFTWARE IS PROVIDED "AS IS", WITHOUT WARRANTY OF ANY KIND,
 * EXPRESS OR IMPLIED, INCLUDING BUT NOT LIMITED TO THE WARRANTIES OF
 * MERCHANTABILITY, FITNESS FOR A PARTICULAR PURPOSE AND
 * NONINFRINGEMENT. IN NO EVENT SHALL THE AUTHORS OR COPYRIGHT HOLDERS BE
 * LIABLE FOR ANY CLAIM, DAMAGES OR OTHER LIABILITY, WHETHER IN AN ACTION
 * OF CONTRACT, TORT OR OTHERWISE, ARISING FROM, OUT OF OR IN CONNECTION
 * WITH THE SOFTWARE OR THE USE OR OTHER DEALINGS IN THE SOFTWARE.
 */

#ifndef SI_TRX_DEFS_H
#define SI_TRX_DEFS_H

/**
 * =============================================================================
 *                         COMMAND DEFINITIONS
 * =============================================================================
 */

/**
 * Si Boot Commands
 */
enum {
  SI_CMD_POWER_UP		= 0x02,
};
/**
 * Si Common Commands
 */
enum {
  SI_CMD_NOP			= 0x00,
  SI_CMD_PART_INFO		= 0x01,
  SI_CMD_FUNC_INFO		= 0x10,
  SI_CMD_SET_PROPERTY		= 0x11,
  SI_CMD_GET_PROPERTY		= 0x12,
  SI_CMD_GPIO_PIN_CFG		= 0x13,
  SI_CMD_FIFO_INFO		= 0x15,
  SI_CMD_GET_INT_STATUS		= 0x20,
  SI_CMD_REQUEST_DEVICE_STATE	= 0x33,
  SI_CMD_CHANGE_STATE		= 0x34,
  SI_CMD_READ_CMD_BUFF		= 0x44,
  SI_CMD_FRR_A_READ		= 0x50,
  SI_CMD_FRR_B_READ		= 0x51,
  SI_CMD_FRR_C_READ		= 0x53,
  SI_CMD_FRR_D_READ		= 0x57,
};
/**
 * Si Tx Commands
 */
enum {
  SI_CMD_START_TX		= 0x31,
  SI_CMD_WRITE_TX_FIFO		= 0x66,
};
/**
 * Si Rx Commands
 */
enum {
  SI_CMD_PACKET_INFO		= 0x16,
  SI_CMD_GET_MODEM_STATUS	= 0x22,
  SI_CMD_START_RX		= 0x32,
  SI_CMD_RX_HOP			= 0x36,
  SI_CMD_READ_RX_FIFO		= 0x77,
};
/**
 * Si Advanced Commands
 */
enum {
  SI_CMD_GET_ADC_READING	= 0x14,
  SI_CMD_PROTOCOL_CFG		= 0x18,
  SI_CMD_GET_PH_STATUS		= 0x21,
  SI_CMD_GET_CHIP_STATUS	= 0x23,
};

/**
 * =============================================================================
 *                         COMMAND ARGUMENTS
 * =============================================================================
 */

/**
 * Si Power Up
 */
enum {
  SI_POWER_UP_FUNCTION		= 0x01,
  SI_POWER_UP_XTAL		= 0x00,
  SI_POWER_UP_TCXO		= 0x01,
};

/**
 * Si GPIO configuration
 */
typedef uint8_t si_gpio_t;
enum {
  SI_GPIO_PIN_CFG_PULL_ENABLE 			= 0x40, /* enable or disable pull-up resistor */
  SI_GPIO_PIN_CFG_GPIO_MODE_DONOTHING		= 0x00, /* pin behaviour is not changed */
  SI_GPIO_PIN_CFG_GPIO_MODE_TRISTATE		= 0x01, /* input and output drivers are disabled */
  SI_GPIO_PIN_CFG_GPIO_MODE_DRIVE0		= 0x02, /* CMOS output "low" */
  SI_GPIO_PIN_CFG_GPIO_MODE_DRIVE1		= 0x03, /* CMOS output "high" */
  SI_GPIO_PIN_CFG_GPIO_MODE_INPUT		= 0x04, /* GPIO is input, for TXDATA etc, function is not configured here */
  SI_GPIO_PIN_CFG_GPIO_MODE_32K_CLK		= 0x05, /* outputs the 32kHz CLK when selected in CLK32_CLK_SEL */
  SI_GPIO_PIN_CFG_GPIO_MODE_BOOT_CLK		= 0x06, /* outputs boot clock when SPI_ACTIVE */
  SI_GPIO_PIN_CFG_GPIO_MODE_DIV_CLK		= 0x07, /* outputs divided xtal clk */
  SI_GPIO_PIN_CFG_GPIO_MODE_CTS			= 0x08, /* output, '1' when device is ready to accept new command */
  SI_GPIO_PIN_CFG_GPIO_MODE_INV_CNT		= 0x09, /* output, inverted CTS */
  SI_GPIO_PIN_CFG_GPIO_MODE_CMD_OVERLAP		= 0x0a, /* output, '1' if a command was issued while not ready */
  SI_GPIO_PIN_CFG_GPIO_MODE_SDO			= 0x0b, /* output, serial data out for SPI */
  SI_GPIO_PIN_CFG_GPIO_MODE_POR			= 0x0c, /* output, '0' while in POR state */
  SI_GPIO_PIN_CFG_GPIO_MODE_CAL_WUT		= 0x0d, /* output, '1' on expiration of wake up timer */
  SI_GPIO_PIN_CFG_GPIO_MODE_WUT			= 0x0e, /* wake up timer output */
  SI_GPIO_PIN_CFG_GPIO_MODE_EN_PA		= 0x0f, /* output, '1' when PA is enabled */
  SI_GPIO_PIN_CFG_GPIO_MODE_TX_DATA_CLK		= 0x10, /* data clock output, for TX direct sync mode */
  SI_GPIO_PIN_CFG_GPIO_MODE_TX_DATA		= 0x11, /* data output from TX FIFO, for debugging purposes */
  SI_GPIO_PIN_CFG_GPIO_MODE_IN_SLEEP		= 0x12, /* output, '0' when in sleep state */
  SI_GPIO_PIN_CFG_GPIO_MODE_TX_STATE		= 0x13, /* output, '1' when in TX state */
  SI_GPIO_PIN_CFG_GPIO_MODE_TX_FIFO_EMPTY	= 0x14, /* output, '1' when FIFO is empty */
  SI_GPIO_PIN_CFG_GPIO_MODE_LOW_BATT		= 0x15, /* output, '1' if low battery is detected */
  SI_GPIO_PIN_CFG_NIRQ_MODE_DONOTHING		= 0x00,
  SI_GPIO_PIN_CFG_SDO_MODE_DONOTHING		= 0x00,
  SI_GPIO_PIN_CFG_DRV_STRENGTH_HIGH		= (0x00 << 5),
  SI_GPIO_PIN_CFG_DRV_STRENGTH_MED_HIGH		= (0x01 << 5),
  SI_GPIO_PIN_CFG_DRV_STRENGTH_MED_LOW		= (0x02 << 5),
  SI_GPIO_PIN_CFG_DRV_STRENGTH_LOW		= (0x03 << 5),
};
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

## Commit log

2014-06-25 Initial commit of hardware designs
    [fbri.brd, fbri.sch]
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2014-07-13 Started work on development hardware
    [fbri_development.brd, fbri_development.sch, fbri_flight.brd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]
2014-07-23 Before trying Direct Tie Tx/Rx
    [fbri_development.brd, fbri_development.sch, fbri_flight_straight.brd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]
2014-07-26 Nearly there, about to re-work MAX1947
    [fbri_development.brd, fbri_development.sch, fbri_flight_straight.brd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]
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2014-07-26 Initial order to hackvana
    [fbri_development.brd, fbri_development.sch, fbri_flight.brd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]
2014-07-26 Added actual board files for version sent to hackvana
    [bristol_longshot.brd, bristol_longshot.sch, bristol_longshot_development.brd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]
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2014-08-23 Such commit. Many change.
    GPS now seems to be alive on the dev board, using UBX mode. SAM D20 drivers coming along.
    Timepulse next. And then radio
    [bristol_longshot.brd, bristol_longshot_development.sch]
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2014-09-08 Board revision 0.96.0 sent
    [bristol_longshot.brd, bristol_longshot.sch]
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2014-10-02 Made all board layers visible
    [bristol_longshot.brd]
2014-10-05 Removed out of data dc-dc converter notes
    [bristol_longshot.sch]
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2014-10-24 [Bugfix] Use latest GPS fix in transmission
    [main.c]
2014-10-24 [Recfactor] Re-enabled internal watchdog, temporary fix
    [hw_config.h, main.c]
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2014-10-24 [Ooops] Fixed comment in watchdog driver
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2014-11-18 [Refactor] Completed replacement of Si4060 with si_trx
    [main.c, si_trx_defs.h]
2014-11-27 [New Feature] Added possiblity to clock symbol timer off the TXCO, but it's disabled and not working on hardware
    [main.c]
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2015-02-21 [New Feature] First revision of development board for solar
    [bristol_longshot.brd, bristol_longshot.sch]
2015-02-25 Added note about Ct on supervisor
    [bristol_longshot.brd, bristol_longshot.sch]
2015-02-25 Added !MR link to cortex debug connex, allows programming but not debugging of boards with watchdog enabled
    Boards with watchdogs mounted can be programmed by holding !MR low. On blackmagic `mon conn e`
    [bristol_longshot.brd, bristol_longshot.sch]
2015-02-25 [Ooops] Hadn't quite aligned that track
    [bristol_longshot.brd]
2015-02-26 Added pdf of breakout
    [bristol_longshot.brd, bristol_longshot.sch]
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2015-03-07 Added contestia checking function to beat checksum bug, added spacing after rsid
    [main.c]
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2015-03-15 Measure error of xosc in hz relative to gps timepulse
    [main.c]
2015-03-16 Sample si temperature at end of transmissions. Fixes broken si temperature
    [main.c]
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2015-03-16 Fixed bug in powersave mode: timepulse output appears to switch back to 1Hz automatically
    [hw_config.h]
2015-03-26 Second revision. Modifications:
    -Ref des inductors for mppt
    -Pull-up on tank en
    -Li-ion charger to LT4054
    -Add TVS diods for mppt
    -Capacitors both sides of jumpers
    -More current in Vctrl divider. TODO partslist for this
    -Fixed cream on supervisor
    [bristol_longshot.brd, bristol_longshot.sch]
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2015-04-02 Various aprs tidy / fix. Added useful resources list. Added telemetry terminate at end of packet
    [ax25.c, main.c]
2015-04-02 Option for not using external oscillator
    [hw_config.h]
2015-04-14 Actually fix things from the last merge
    [hw_config.h]
2015-05-12 Fix a couple of things in geofence, including adding consts
2015-05-13 Bugfix: Fix rsid pwm
2015-05-13 Dropped clock rate back to 4MHz, fixes startup issues
    [main.c]
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2015-05-14 Moved main hardware into subfolder
    [bristol_longshot.brd, bristol_longshot.sch, bristol_longshot_development.brd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]
2015-05-14 Added partslist, updated parts for back-aaa
    [bristol_longshot.brd, bristol_longshot.sch]
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2015-05-14 Added cream to battery contacts on aaa-board
    [bristol_longshot.brd, bristol_longshot.sch]
2015-05-15 Much layout done for new frontpanel
    [bristol_longshot.brd, bristol_longshot.sch]
2015-05-16 Routing on the bottom half of the main board almost done
    [bristol_longshot.brd, bristol_longshot.sch]
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2015-06-09 Moved to single-board solar tracker. Parts lists out of date!
    [bristol_longshot.brd, bristol_longshot.sch, bristol_longshot_development.brd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]
2015-06-09 Added programming adaptors. Parts lists out of date!
    [bristol_longshot.brd, bristol_longshot.sch]
2015-06-09 Added aaa battery version 0.982.0. Parts list still out of date
    [bristol_longshot.brd, bristol_longshot.sch]
2015-06-09 Added LPS3015 mppt inductor footprint alongside XAL6060 footprint
    [bristol_longshot.brd, bristol_longshot.sch]
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2015-06-12 Updated main solar active components names to correspond with partslist
    [bristol_longshot.brd, bristol_longshot.sch]
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2015-06-15 Renamed test case main to avoid clash with other main.c, always rebuild source for testcases, show full debug trace during testcases (keepin' it real)
2015-06-15 Updated many parts lists, updated bard numbering, removed makefiles for inactive things
    [bristol_longshot.brd, bristol_longshot.sch]
2015-06-17 Re-size output pngs to be a bit more reasonably sized
    [bristol_longshot.brd]
2015-06-18 [UBSEDS8] Oscillator issues, disabling tcxo offset field and set to use internal osc for timing rather than tcxo
    [hw_config.h, main.c]
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2015-06-20 Finally moved to emacs24, still using gdb-ui though
    To use gdb-ui rather than the broken gdb-mi you'll need to:
    - Grab `gdb-ui.el` and `gdb-ui.elc` from emacs 23 source
    - Put them in your load path somewhere
    - `(require 'gdb-ui)` in your init
2015-06-20 Revert "[UBSEDS8] Oscillator issues, disabling tcxo offset field and set to use internal osc for timing rather than tcxo"
    This reverts commit aa8976eaf1311833cc78012bb4701167ed26bbf5.
    [hw_config.h, main.c]
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2015-06-25 RF power set in hw_config, full power for APRS. RF tests in separate file, aprs shuts stops on error correctly
    [hw_config.h, main.c]
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2015-06-25 Switched tc5 aprs to 16-bit mode to reduce error. Reduced pre-scaler
    [ax25.c]
2015-06-25 Doubled the frequency of GCLK1. Doubles the resoultion of the tcxo error measurement
    [hw_config.h]
2015-06-26 Fixed APRS pre-emphasis using custom FIR filter. Not sure on the deviation yet but it looks good in audacity
    [si_trx_defs.h]
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2015-06-28 [Bugfix] Memory HOLD pin needs to be high. Also adjusted pad/cream size. Bump to V0.98x.1
    [bristol_longshot.brd, bristol_longshot.sch]
2015-06-28 Fixed memory pin names to correspond with the datasheet
    [bristol_longshot.sch]
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2015-06-29 location_aprs test now uses pre-defined list of interesting locations
    [location_aprs_tc_list.csv]
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2015-06-29 Added vias though all the pads on the debug connector
    [bristol_longshot.brd, bristol_longshot.sch]
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2015-06-29 Fix point_in_poly. We need to interpolate along diagonal boarder lines which is kinda going to need floating point
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2015-07-03 Brought up gps on new hw, various bugfix, pre-calculate telemetry timer counts and more
    [hw_config.h, main.c]
2015-07-04 Increase the frequency of the internal watchdog gclk so we don't get massive lag when kicking it. Also fix up varous timing issues / speed things up
    [hw_config.h]
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2015-07-11 Fixed a couple of APRS timing/format issues. APRS txes after rtty, on 144.8 when geofence is disabled
    [main.c]
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2015-07-12 Fixed solar adc reading
    [analogue.c]
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2015-07-18 Fix xosc error for earlier change to double edged gps timepulse events.
    Xosc measurement now takes 0.5s, resolution is 4Hz again
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2015-07-22 Added no telemetry geofence for China, NK and Yemen. Added test case
    [location_telemetry_tc_list.csv]
2015-07-24 Fix location_aprs_file test case for integer params
2015-07-31 Added python parser for raw pico tracker data.
    I haven't rigorously tested it, but the fact that the data starts in
    Montpelier on the 25th, and it correctly decodes the APRS test longitude of
    '<*e7' to -72.75 degrees is promising.
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2015-09-13 Updated main tracker solar design to use a LTC3105 energy harvester for solar and a 3V primary lithium for backup. Work in Progress
    [bristol_longshot.brd, bristol_longshot.sch]
2015-09-14 More work on LTC3105 / primary 3V lithium board. Still work in progress
    Needs solder pads and switch for 3V lithium battery.
    [bristol_longshot.brd, bristol_longshot.sch]
2015-09-15 Added new "simple" solar/primary design that just uses a LTC3105. Designed for use with a 1.5V primary lithium source.
    Parts list is work in progress.
    [bristol_longshot.brd, bristol_longshot.sch]
2015-09-15 Updated schematic labels, fixed R11 value
    [bristol_longshot.brd, bristol_longshot.sch]
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2015-09-15 Final board changes for solar/primary lithium AAA (v0.985.0)
    [bristol_longshot.brd]
2015-09-18 Added DNP/0Ω for when using battery only on main-solar-simple
    [bristol_longshot.brd, bristol_longshot.sch]
2015-09-21 Hardware V0.985.2, replaces BMP180 with MS5607
    [bristol_longshot.brd, bristol_longshot.sch]
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2015-09-29 main-solar-simple: Fixed mouser part nr for wdt, fixed memory label on schematic
    [bristol_longshot.sch]
2015-09-30 main-solar_simple: Updated board logos and gps antenna soldermask on v0.985.2
    [bristol_longshot.brd]
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2015-10-08 Hardware v0.985.3, reduce external thermistor holes to 0.5mm dia
    [bristol_longshot.brd, bristol_longshot.sch]
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2015-10-09 Add BMP180 to data.c, format output correctly
    [main.c]
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2015-10-11 Disable accululation, doesn't appear to do anything useful
    [analogue.c]
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2015-10-28 Add low-power SE880-based design with side mounted GPS antenna. v0.986.0
    Will side mounted attenna cause problems with fading as the payload rotates?
    TODO: Labels, couple of airwires, more testing on current hardware
    [bristol_longshot.brd, bristol_longshot.sch]
2015-10-28 [low-power-side] More work on board, vaguely complete. Added parts list
    [bristol_longshot.brd, bristol_longshot.sch]
2015-10-30 Added low-power breakout board for testing. 80x80mm
    "Possibly the worst pcb design in the world"
    [bristol_longshot.brd, bristol_longshot.sch]

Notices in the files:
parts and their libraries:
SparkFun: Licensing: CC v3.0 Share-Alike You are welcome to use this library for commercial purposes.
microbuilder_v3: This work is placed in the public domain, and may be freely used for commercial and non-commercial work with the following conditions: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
